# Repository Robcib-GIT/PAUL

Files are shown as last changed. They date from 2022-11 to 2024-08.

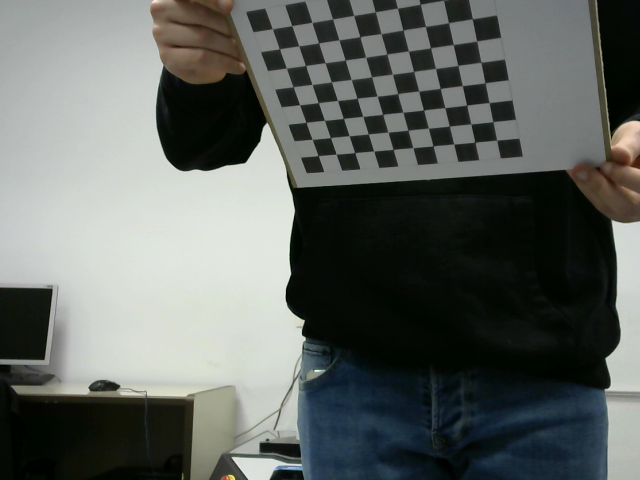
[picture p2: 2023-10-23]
Docs/Assets/Raúl/Calibracion/Fotos/Image35.png

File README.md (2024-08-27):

# Pneumatic Actuated Ultrasoft Limb (PAUL)

In this repository you will find all the code necessary for the control of the PAUL soft robot. Due to the problems that can be associated with working with it and the difficulty of building it, it is also possible to work using a built-in simulator. The programming language used is Matlab.





## Available videos ##

- [Manufacturing Process](https://www.youtube.com/watch?v=WlBE3JDpxWw)
- [General Working](https://www.youtube.com/watch?v=1XM6AjTwlqs)
- [One Module Control](https://www.youtube.com/watch?v=sqhGBfGOFts)

## Inverse Kinematics ##

We are currently working on the development of several inverse kinematics methods. We will post updates here when they reach a first functional level.

Although we are open to explore different possibilities, we consider, for the moment, to use optimisation-based algorithms (such as CCD or FABRIK), search methods (type A*), genetic algorithms and, of course, reinforcement learning.

### Genetic Algorithm

The algorithm developed here achieves errors of less than 1mm with execution times fast enough for soft robots. Contrary to what happens in many methodologies, the algorithm allows the position of the robot's intermediate modules to be chosen.

The hyperparameters have been decided starting from those established [in this work](https://www.mdpi.com/2075-1702/11/10/952) and then making small variations with the aim of finding a solution capable, at the same time, of achieving good precision in low times.

The following table shows the results of the hyperparameter optimisation. The number of individuals and elitism and mutation rates have been varied. For each hyperparameter setup, the algorithm has been runned 40 times. For all of them, median error and execution time have been compared for the genetic algorithm without shape control.

<details>
  <summary><strong>Hyperparameter optimisation table</strong></summary>
  <table>
    <thead>
    <tr>
    <th># of individuals</th>
    <th>Parents&#39; rate</th>
    <th>Mutation rate</th>
    <th>Median error (mm)</th>
    <th>Median time (s)</th>
    </tr>
    </thead>
    <tbody>
    <tr>
    <td>25</td>
    <td>0.1</td>
    <td>0.7</td>
    <td>1.30</td>
    <td>3.68</td>
    </tr>
    <tr>
    <td>25</td>
    <td>0.1</td>
    <td>0.8</td>
    <td>1.33</td>
    <td>3.91</td>
    </tr>
    <tr>
    <td>25</td>
    <td>0.2</td>
    <td>0.7</td>
    <td>1.31</td>
    <td>3.42</td>
    </tr>
    <tr>
    <td>25</td>
    <td>0.2</td>
    <td>0.8</td>
    <td>1.36</td>
    <td>3.42</td>
    </tr>
    <tr>
    <td>25</td>
    <td>0.3</td>
    <td>0.7</td>
    <td>1.07</td>
    <td>3.05</td>
    </tr>
    <tr>
    <td>25</td>
    <td>0.3</td>
    <td>0.8</td>
    <td>1.99</td>
    <td>3.14</td>
    </tr>
    <tr>
    <td>50</td>
    <td>0.1</td>
    <td>0.7</td>
    <td>0.91</td>
    <td>6.19</td>
    </tr>
    <tr>
    <td>50</td>
    <td>0.1</td>
    <td>0.8</td>
    <td>0.90</td>
    <td>4.56</td>
    </tr>
    <tr>
    <td><strong>50</strong></td>
    <td><strong>0.2</strong></td>
    <td><strong>0.7</strong></td>
    <td><strong>0.88</strong></td>
    <td><strong>4.31</strong></td>
    </tr>
    <tr>
    <td>50</td>
    <td>0.2</td>
    <td>0.8</td>
    <td>0.88</td>
    <td>4.81</td>
    </tr>
    <tr>
    <td>50</td>
    <td>0.3</td>
    <td>0.7</td>
    <td>0.99</td>
    <td>6.12</td>
    </tr>
    <tr>
    <td>50</td>
    <td>0.3</td>
    <td>0.8</td>
    <td>0.90</td>
    <td>5.03</td>
    </tr>
    <tr>
    <td>75</td>
    <td>0.1</td>
    <td>0.7</td>
    <td>0.86</td>
    <td>5.40</td>
    </tr>
    <tr>
    <td>75</td>
    <td>0.1</td>
    <td>0.8</td>
    <td>0.82</td>
    <td>5.37</td>
    </tr>
    <tr>
    <td>75</td>
    <td>0.2</td>
    <td>0.7</td>
    <td>0.84</td>
    <td>5.75</td>
    </tr>
    <tr>
    <td>75</td>
    <td>0.2</td>
    <td>0.8</td>
    <td>0.71</td>
    <td>5.95</td>
    </tr>
    <tr>
    <td>75</td>
    <td>0.3</td>
    <td>0.7</td>
    <td>0.82</td>
    <td>6.52</td>
    </tr>
    <tr>
    <td>75</td>
    <td>0.3</td>
    <td>0.8</td>
    <td>0.85</td>
    <td>6.58</td>
    </tr>
    <tr>
    <td>100</td>
    <td>0.1</td>
    <td>0.7</td>
    <td>0.79</td>
    <td>5.17</td>
    </tr>
    <tr>
    <td>100</td>
    <td>0.1</td>
    <td>0.8</td>
    <td>0.83</td>
    <td>5.14</td>
    </tr>
    <tr>
    <td>100</td>
    <td>0.2</td>
    <td>0.7</td>
    <td>0.74</td>
    <td>5.79</td>
    </tr>
    <tr>
    <td>100</td>
    <td>0.2</td>
    <td>0.8</td>
    <td>0.83</td>
    <td>7.02</td>
    </tr>
    <tr>
    <td>100</td>
    <td>0.3</td>
    <td>0.7</td>
    <td>0.81</td>
    <td>8.19</td>
    </tr>
    <tr>
    <td>100</td>
    <td>0.3</td>
    <td>0.8</td>
    <td>0.87</td>
    <td>7.55</td>
    </tr>
    </tbody>
  </table>
 
</details>

## Directory index ##

- Code_arduino: Arduino code for controlling the pneumatic actuation bench, which sends the necessary compressed air to move the robot.
- Code_matlab: Matlab code. It includes the control interface, where one can control everything related to computer vision, communications between the robot and the computer, the actuation signals, etc.
- CAD: Everything related to the CAD designs, from the molds to the joints of the robot. They were designed using Autodesk Fusion 360.
- Memoria: Everything related to the thesis documentation.

## Published works ##

García-Samartín, J.F.; Rieker, A.; Barrientos, A. Design, Manufacturing, and Open-Loop Control of a Soft Pneumatic Arm. _Actuators_ **2024**, 13, 36. https://doi.org/10.3390/act13010036

García-Samartín, J.F.; Molina-Gómez, R.; Barrientos, A. Model-Free Control of a Soft Pneumatic Segment. _Biomimetics_ **2024**, 9, 127. https://doi.org/10.3390/biomimetics9030127

García-Samartín, J.F., del Cerro, J., Barrientos, A. Inverse kinematic modelling with shape control of a soft robot using genetic algorithms. _Jornadas de Automática_ **2024**, 45. https://doi.org/10.17979/ja-cea.2024.45.10968

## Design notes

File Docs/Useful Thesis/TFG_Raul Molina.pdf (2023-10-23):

# SENSORIZACIÓN Y CONTROL DE UN ROBOT BLANDO

# MANIPULADOR

SEPTIEMBRE 2023

## Raúl Molina Gómez

DIRECTORES DEL TRABAJO FIN DE GRADO:

## Antonio Barrientos Cruz Jorge F. García-Samartín

## Raúl Molina Gómez

### TRABAJO FIN DE GRADOPARA LA OBTENCIÓN DEL TÍTULO DE GRADUADO EN INGENIERÍA EN TECNOLOGÍAS INDUSTRIALES

### Universidad Politécnica de Madrid

### Escuela Técnica Superior de Ingenieros Industriales

## Grado en Ingeniería en Tecnologías Industriales

### Trabajo Fin de Grado

## Sensorización y Control de un Robot Blando Manipulador

### Autor: Raúl Molina Gómez

### Tutor Académico: Antonio Barrientos Cruz

### Cotutor: Jorge F. García-Samartín

### septiembre, 2023

ii

# Agradecimientos

En primer lugar, quiero expresar mi agradecimiento a todas las personas cuyo apoyo ha sido muy valioso para mí tanto durante la realización de este proyecto como durante todos mis estudios universitarios.
Agradezco a mis padres por haberme brindado siempre la mejor educación posible, por haberme ayudado cuando más lo necesitaba y por los excelentes valores personales basados en el esfuerzo, el respeto y la humildad que me han inculcado.
Agradezco a mi hermana por su ayuda y apoyo durante toda la carrera universitaria. Agradezco también a todos mis amigos y compañeros de carrera, pues sin ellos no sería quien soy actualmente.

Asimismo, quiero agradecer a todas aquellas personas que me han ayudado a llevar a cabo este proyecto.
Agradezco a Antonio Barrientos, por confiar en mí y darme la oportunidad de realizar este Trabajo Fin de Grado en el laboratorio Robcib. También quiero agradecer su ayuda y la motivación que me ha dado en los momentos de mayor desesperación.
Agradezco de manera especial a Jorge García-Samartín por su paciencia, amabilidad, tiempo y guía durante este trabajo. Sin ti no habría sido posible completar este proyecto. Agradezco también a todos los que me habéis acompañado durante toda la realización del proyecto en el laboratorio Robcib. Chrystian, David e Ysmaldo, me habéis acogido como un doctorando más y me habéis ayudado a conseguir este logro creando un clima de trabajo extraordinario.

Raúl Molina Gómez

iii

# Resumen Ejecutivo

En la actualidad, el desarrollo de nuevos robots que permitan realizar y automatizar cada vez más tareas se ha convertido en una prioridad en la industria robótica. Estas investigaciones se enfocan tanto en nuevos sistemas de control como en el diseño y fabricación de robots con nuevos materiales. Es así como surge hace aproximadamente 20 años un nuevos campo de la robótica: la robótica blanda o Soft Robotics.

Este nuevo tipo de robots surge con el objetivo de crear máquinas cuyas propiedades y comportamiento se asemejen a los organismos biológicos y tejidos blandos. Este nuevo enfoque se aleja completamente del concepto de robótica que se venía empleando en las épocas pasadas, pues no se usan para su construcción materiales rígidos.

Estos factores en su diseño y estructura les otorgan una gran ventaja: son capaces de interactuar de manera segura y eficiente con entornos cambiantes y complejos. Esto permite su uso en múltiples aplicaciones hasta ahora extremadamente complejas de realizar, como el trabajo con humanos o la adaptación a terrenos de difícil acceso para un robot móvil tradicional. Un ejemplo de esto último serían los escombros de un edificio o tuberías estrechas y serpenteantes.

Son todas estas potenciales aplicaciones para la sociedad las que motivan la investigación acerca de esta nueva tecnología, como es el caso de este proyecto. Así, el objetivo que presenta este Trabajo Fin de Grado es el de realizar sobre el diseño del Robot PAUL, fruto del trabajo de Adrián Rieker [1], un sistema de control en posición en cadena cerrada para uno de los segmentos que lo componen. Para ello se precisa además modificar ciertos aspectos del robot, como su diseño o proceso de fabricación, así como seleccionar y caracterizar el método de sensorización a emplear.

Cabe señalar que el Robot PAUL se compone de varios módulos blandos en serie, cada uno de los cuales es actuado mediante 3 vejigas neumáticas que, al deformarse por efecto del aire a presión que se introduce en ellas, consiguen modificar la forma del módulo. Para lograrlo, y debido a la falta de sensores de presión, la cantidad de aire comprimido introducido en cada módulo se regula mediante el tiempo de apertura de los circuitos de

v

vi RESUMEN EJECUTIVO

admisión y escape del aire. A este tiempo de apertura se le ha denominado como tiempo de actuación.
Para completar el bucle de control en cadena cerrado se han empleado unos sensores resistivos elastómeros comerciales (figura R1), fabricados por la empresa Adafruit [2]. Estos sensores permiten medir cambios en sus resistencias producidos por variaciones en su longitud. De esta forma, se mide de manera indirecta la deformación y forma final de cada uno de los segmentos del robot a los que están fijos.

Figura R1 Sensores empleados para el sistema de control en cadena cerrada del robot. Fuente [2]

Estas medidas se realizan gracias a un hardware específico de medición y monitoreo de parámetros eléctricos denominado INA3221. Este dispositivo permite obtener medidas de tensión, corriente y/o potencia con elevada precisión gracias a un filtro paso bajo y un convertidor analógico-digital. Además, cuenta con tres canales de medida, con lo que se pueden realizar mediciones de los tres sensores que incorpora cada segmento. Así, la técnica empleada consiste en alimentar mediante una fuente de tensión un divisor de tensiones compuesto por una resistencia fija y un sensor, lo que permite medir las variaciones de tensión que sufre el sensor cuando se produce la actuación y correspondiente deformación del segmento.
Asimismo, para la caracterización de los sensores se ha diseñado y construido un banco de pruebas (figura R2) que estira de manera constante y uniforme el sensor. De esta forma se puede extraer la relación entre la tensión medida y su variación de longitud. A su vez, para su fijación e implementación en el robot, se ha usado un sellador adhesivo de silicona denominado comercialmente DOWSIL 732.

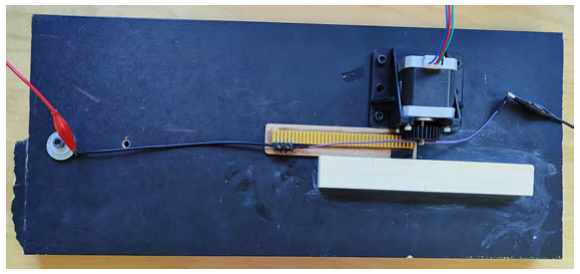
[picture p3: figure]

Figura R2 Banco de pruebas diseñado para caracterizar el comportamiento de los sensores. Fuente: elaboración propia

SENSORIZACIÓN Y CONTROL DE UN ROBOT BLANDO MANIPULADOR RAÚL MOLINA GÓMEZ

RESUMEN EJECUTIVO vii

Por su parte, el sistema de control emplea el diagrama de bloques de la figura R3 para que, mediante la introducción de un punto objetivo contenido en el espacio de trabajo del robot, se consiga mover dicho robot al punto deseado obteniendo un error mínimo. Este sistema surge como resultado de numerosas pruebas e iteraciones de búsqueda y perfeccionamiento del método de control adecuado. La justificación a este largo proceso es la complejidad presente en el modelado de los Soft Robots, pues su estructura continua y maleable les otorga una característica nunca vista en la robótica tradicional que es la inexistencia de cadena cinemática, o lo que es lo mismo, se podría considerar que estos robots presentan infinitos grados de libertad.

Figura R3 Diagrama de bloques empleado para el control del segmento. Fuente: elaboración propia

La resolución a este problema finalmente pasa por el entrenamiento de dos redes neuronales prealimentadas o feedfoward. En el caso de la primera de ellas (la denominada como NN1), transforma los valores de posición introducidos en tiempos de actuación objetivo, mientras que la segunda (NN2) convierte las mediciones de tensión en tiempos de actuación del robot. Así, se suprime la necesidad de un regulador multivariable. Para su obtención, es necesario realizar el entrenamiento de las redes usando múltiples datos contenidos en datasets del comportamiento del robot. Así, se ha diseñado además un método de obtención de estos datos (tensiones, posiciones y tiempos) de forma automática, basado en el método de captura de posiciones por visión con computador ideado por Adrián Rieker [1]. Uno de los resultados de esta captura de datos se ve en la figura R4, que muestra el espacio de trabajo del robot.

Figura R4 Espacio de trabajo del robot desarrollado. Fuente: elaboración propia

UNIVERSIDAD POLITÉCNICA DE MADRID ESCUELA TÉCNICA SUPERIOR DE INGENIEROS INDUSTRIALES

viii RESUMEN EJECUTIVO

Durante esta fase del proyecto, se observaron además múltiples problemas relacionados con el diseño y la fabricación del robot, como las numerosas fugas de aire que se producían. Es por ello que se acometieron como un objetivo adicional del trabajo modificaciones en el diseño, la programación y el proceso de fabricación del robot.
Finalmente, y tras las numerosas iteraciones de obtención de datos y diseño y entrenamiento de las redes, se procedió a realizar varias pruebas y experimentos para verificar el cumplimiento de los objetivos. Los resultados obtenidos fueron muy satisfactorios, logrando errores de en torno a los 5mm, obteniendo así un robot que incluso supera en precisión a otros robots similares desarrollados en la literatura.
Con todo ello, el trabajo final realizado se puede ver en la figura R5.

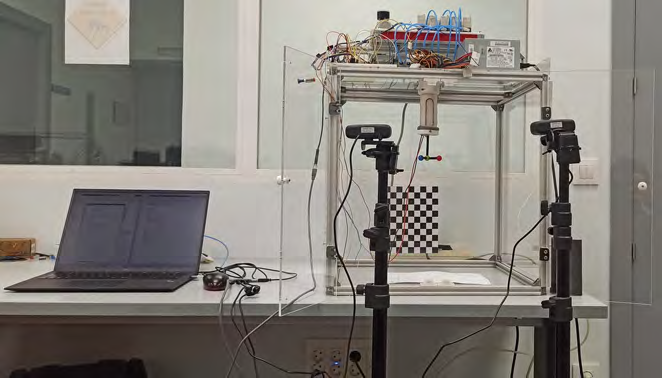
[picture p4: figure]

Figura R5 Imagen del entorno del robot durante su desarrollo. Fuente: elaboración propia

Códigos UNESCO

1203 Ciencia de los ordenadores 1203.04 Inteligencia Artificial 1203.25 Diseño de sistemas sensores 3304 Tecnología de los ordenadores 3304.12 Dispositivos de control
3304.19 Robótica
3311 Tecnología de la Instrumentación 3311.01 Tecnología de la automatización 3311.02 Ingeniería de control
3311.07 Instrumentos electrónicos

Palabras clave

Robótica blanda, Soft Robot, manipulador, sensor resistivo elastómero, red neuronal, feedforward neuronal network, control en posición, MATLAB, Arduino, silicona.

SENSORIZACIÓN Y CONTROL DE UN ROBOT BLANDO MANIPULADOR RAÚL MOLINA GÓMEZ

# Índice

Índice de Figuras | xvi
Índice de Tablas | xvii
1. Introducción | 1
2. Estado del arte | 7
2.2.3. Métodos experimentales. Métodos basados en el entrenamiento de
3. Estudio y caracterización de los sensores | 29

ix

x RESUMEN EJECUTIVO

3.3. Caracterización del comportamiento de los sensores | 36
3.3.1. Cambio de comportamiento de los sensores | 36
3.3.2. Diseño y construcción del banco de pruebas | 39
3.3.3. Conclusiones extraídas del comportamiento de los sensores | 43
3.4. Instrumentación final e implementación de los sensores en el robot | 45
3.4.1. Justificación de la elección del método de fijación de los sensores . . 45
3.4.2. Instrumentación y montaje final | 48
4. Herramientas utilizadas | 51
4.1. Deep Learning Toolbox de MATLAB | 51
4.2. Redes Neuronales Prealimentadas (Feedforward Neural Network) | 53
4.2.1. Funcionamiento de una red neuronal prealimentada | 53
4.2.2. Redes Neuronales Feedforward en MATLAB | 57
4.3. Redes Neuronales de tipo LTSM | 59
4.3.1. Arquitectura Básica de una Celda LSTM | 60
4.3.2. Implementación Práctica en MATLAB | 61
5. Modificaciones del diseño, fabricación y control de los segmentos | 63
5.1. Cambios en el proceso de fabricación | 63
5.1.1. Cambio de posición de las vejigas | 64
5.1.2. Método de sellado de fugas | 65
5.1.3. Eliminación del espacio interno del segmento | 66
5.1.4. Cambio de forma de los machos de cera | 67
5.2. Cambios en el diseño | 68
5.2.1. Nuevas piezas | 69
5.3. Cambios en la forma de control del robot | 72
6. Diseño y desarrollo del sistema de control para un segmento | 75
6.1. Introducción | 75
6.2. La clase Robot | 75
6.2.1. Código Arduino | 80
6.3. Planteamiento inicial del problema - Control analítico | 82
6.4. Segundo intento de resolución del problema - Control experimental . . . . 85
6.4.1. Obtención de la red neuronal a emplear | 86
6.4.2. Diseño del regulador PID | 93
6.4.3. Conclusiones | 94
6.5. Resolución y planteamiento final del problema | 95
6.5.1. Esquema de control final | 95
6.5.2. Obtención de la red neuronal a emplear | 96
6.5.3. Conclusiones y resultados | 98

SENSORIZACIÓN Y CONTROL DE UN ROBOT BLANDO MANIPULADOR RAÚL MOLINA GÓMEZ

ÍNDICE xi

6.5.4. Descarte del uso de redes LSTM | 99
6.6. Control del robot | 100
6.6.1. Métodos para el movimiento del segmento | 100
6.6.2. Procedimiento de uso | 102
7. Pruebas y Resultados | 103
7.1. Experimentos de posicionamiento | 104
7.1.1. Primer experimento | 104
7.1.2. Segundo experimento | 105
7.1.3. Tercer experimento | 107
7.2. Experimentos de estudio de la modularidad | 109
8. Conclusiones y líneas futuras | 113
8.1. Conclusiones | 113
8.2. Líneas futuras | 115
Bibliografía | 117
A. Estudio de impacto ambiental, social, ético y legal | 123
A.1. Impacto ambiental | 123
A.1.1. Impacto social | 125
A.1.2. Impacto ético | 125
A.1.3. Impacto legal | 126
A.1.4. Conclusión: ODS | 126
B. Planificación temporal y presupuesto | 127
B.1. Estructura de Descomposición del Proyecto | 127
B.2. Planificación | 128
B.3. Presupuesto | 129
B.3.1. Coste material | 129
B.3.2. Coste de amortización | 129
B.3.3. Coste de personal | 130
B.3.4. Presupuesto final | 130
C. Código de interés | 131

UNIVERSIDAD POLITÉCNICA DE MADRID ESCUELA TÉCNICA SUPERIOR DE INGENIEROS INDUSTRIALES

# Índice de Figuras

R1. Sensores empleados para el sistema de control en cadena cerrada del robot.
Fuente [2] | vi

R2. Banco de pruebas diseñado para caracterizar el comportamiento de los
sensores. Fuente: elaboración propia | vi
R3. Diagrama de bloques empleado para el control del segmento. Fuente: ela-
boración propia | vii
R4. Espacio de trabajo del robot desarrollado. Fuente: elaboración propia . . . vii R5. Imagen del entorno del robot durante su desarrollo. Fuente: elaboración
propia | viii
1.1. Aumento de las búsquedas de carácter académico relacionadas con la ro-
bótica blanda. Fuente: Scopus | | 2
1.2. Robot final desarrollado en el trabajo previo de Adrián Rieker. Fuente [1] . | 4
2.1. Clasificación de los sensores con base de hidrogel según su aplicación y
composición. Fuente [5] | 9
2.2. Comportamiento y características de un sensor fabricado con un hidrogel
orgánico. Fuente [6] | 10
2.3. Comportamiento ante el movimiento humano de un sensor hidrogelado.
Fuente [7] | 11
2.4. Propiedades de un sensor con base de hidrogel e iones de hierro. Fuente [8] 11
2.5. Estudio del comportamiento y uso de un sensor elastómero fabricado con
impresión 3D. Fuente [9] | 12
2.6. Estructura esquemática de los MXene, incluyendo los dopados con elementos de transición M y los dopados con elementos ligadores X, y los MAX
de los que provienen. Fuente [12] | 13
2.7. Resultados de un sensor capacitivo realizado con un MXene y una matriz
elastomérica. Fuente [13] | 14

xii

ÍNDICE GENERAL xiii

2.8. Resultados de un sensor flexible piezorresistivo realizado con un MXene.
Fuente [14] | 15
2.9. Ejemplo de funcionamiento de un sensor óptico empleado en robótica blan-
da. Fuente [16] | 16
2.10. Ejemplo de funcionamiento de un sensor magnético empleado en robótica
blanda. Fuente [17] | 17
2.11. Ejemplo de uso y caracterización de un sensor inductivo aplicado a la ro-
bótica blanda. Fuente [18] | 18
2.12. Creación, uso y validación de un sensor basado en corrientes de Foucault.
Fuente [19] | 19
2.13. Los dos pasos necesarios para el modelado de robots blandos: modelado específico (entre el espacio de los actuadores y el de las configuraciones)
y modelado independiente (entre el espacio de configuraciones y el de la
tarea). Fuente [20] | 19
2.14. Principales métodos para el modelado de Soft Robots. Fuente [21] | 21
2.15. Principales métodos para el control de Soft Robots. Fuente [21] | 21
2.16. Modelado y control mediante elementos finitos. Fuente [22] | 22
2.17. Modelado basado en curvatura constante. Fuente [23] | 23
2.18. Control de un Soft Robot actuado con tendones mediante el uso de la teoría
de vigas de Cosserat. Fuente [24] | 24
2.19. Resultados de una simulación realizada para un robot blando manipulador utilizando un modelo basado en la curvatura polinómica de 4º grado. Fuente
[25] | 25
2.20. Resultados del empleo de una red neuronal para conocer la posición de
un robot blando a partir de las medidas de sus sensores de deformación.
Fuente [27] | 26
2.21. Robot blando y su setup para el control con el uso de PCC y aprendizaje
por refuerzo. Fuente [28] | 27
3.1. Sensor resistivo elastómero empleado en el control en cadena cerrada de
PAUL. Fuente [2] | 30
3.2. Microcontrolador Arduino Due empleado. Fuente: elaboración propia . . . 32
3.3. Ruido de la señal medida y su solución por filtrado. Fuente: elaboración
propia | 33
3.4. Selección del hardware de medición. Fuente [29], [30] y [31] | 35
3.5. Comportamiento de un sensor similar al empleado en este proyecto. Fuente
[32] | 38
3.6. Comparación del comportamiento de los sensores comercial y modificado.
Fuente: elaboración propia | 38

UNIVERSIDAD POLITÉCNICA DE MADRID ESCUELA TÉCNICA SUPERIOR DE INGENIEROS INDUSTRIALES

xiv ÍNDICE GENERAL

3.7. Par piñón-cremallera empleado en el banco de pruebas para caracterizar el
3.8. Base de apoyo para anclar y fijar el motor paso a paso en el banco de
3.9. Sistema de anclaje del extremo fijo del sensor a probar. Fuente: elaboración
3.10. Detalles de las conexiones de ambos extremos del sensor a caracterizar.
3.11. Guía para evitar el movimiento lateral de la cremallera. Fuente: elaboración
3.12. Banco de pruebas para la caracterización de los sensores. Fuente: elabora-
3.13. Comportamiento ante la elongación de dos sensores modificados distintos.
3.14. Comportamiento de uno de los sensores modificados ante las distintas tem-
3.15. Sellador de silicona empleado en la fijación de los sensores al robot. Fuente
3.16. Molde y pieza para la prueba de la fijación del sensor a la silicona con el
3.17. Detalle de la fijación de los sensores con el sellador Dowsil 732. Fuente:
3.18. Posición de todos los elementos electrónicos para el posterior control del
3.19. Detalle de las conexiones entre dispositivo de medida y sensor. Fuente:
3.20. Esquema de la conexión entre los dispositivos. Fuente: elaboración propia
4.1. Modelo computacional de red neuronal prealimentada de una sola capa
4.5. Ejemplo de función de costo respecto a los pesos y sesgos de las neuronas.

SENSORIZACIÓN Y CONTROL DE UN ROBOT BLANDO MANIPULADOR RAÚL MOLINA GÓMEZ

ÍNDICE GENERAL xv

4.6. Estructura de una celda de una red neuronal recurrente LSTM, donde los valores de c son los correspondientes a la memoria, h representa las salidas y x las entradas. Las celdas en amarillo son redes neuronales simples con sus funciones de activación y los puntos rosa son operaciones específicas para descartar, actualizar y calcular el nuevo estado oculto de la memoria.
5.1. Comparación de la posición de las cámaras internas de PAUL antes y después de su cambio. Su ubicación se puede deducir a partir de los salientes superiores para introducir los tubos neumáticos que conducen el aire a su
5.2. Detalle de la parte inferior de un segmento. Fuente: elaboración propia . . 65
5.3. Detalle de la fijación de los tubos neumáticos a un segmento del robot.
5.4. Detalle del moldeo de un segmento sin cavidad interna. Fuente: elaboración
5.5. Comparación entre la geometría nueva y antigua de los machos de cera que
5.6. Comparación entre los diseños antiguo y nuevo de la pieza de conexión con
5.8. Comparación entre los diseños antiguo y nuevo de la pieza de conexión
5.9. Comparación entre los diseños antiguo y nuevo de la baliza de captura de
6.3. Esquema de control empleando tabla dinámica y MCI. Fuente: elaboración
6.4. Esquema de control empleando una red neuronal y un regulador PID. Fuen-
6.5. Diagrama del proceso de obtención de datos. Fuente: elaboración propia . . 90
6.6. Diagrama de bloques empleado para el control del segmento. Fuente: ela-
6.7. Diagrama final del proceso de obtención de datos. Fuente: elaboración propia 97
6.8. Resultados del entrenamiento de dos redes LSTM. Fuente: elaboración propia 99

UNIVERSIDAD POLITÉCNICA DE MADRID ESCUELA TÉCNICA SUPERIOR DE INGENIEROS INDUSTRIALES

xvi ÍNDICE DE FIGURAS

7.2. Robot PAUL durante el primer experimento de verificación de su capacidad
7.4. Espacio de trabajo de un segmento del robot PAUL. Fuente: elaboración
7.5. Movimientos realizados por el robot durante el tercer experimento. Fuente:
7.6. Robot PAUL durante el primer experimento del estudio de modularidad.
7.7. Robot PAUL durante el segundo experimento del estudio de modularidad.
7.8. Piezas necesarias para la fabricación de la nueva baliza. Fuente: elaboración

A.1. ODS a los que contribuye este proyecto. Fuente: elaboración propia . . . . 126

B.1. Estructura de Descomposición del Proyecto. Fuente: elaboración propia . . 127

SENSORIZACIÓN Y CONTROL DE UN ROBOT BLANDO MANIPULADOR RAÚL MOLINA GÓMEZ

# Índice de Tablas

3.1. Tabla comparativa de las distintas características del INA219, el INA226 y
el INA3221. Fuente: Elaboración propia | 34
3.2. Principales propiedades del sellador DOWSIL 732 Multi-Purpose Sealant.
Fuente: Adaptación de [34] | 46
7.1. Resultados del primer experimento. Fuente: elaboración propia | 105
7.2. Resultados del segundo experimento. Fuente: elaboración propia | 105
7.3. Resultados de la prueba de realización de figuras. Fuente: elaboración propia 109
7.4. Resultados del experimento con un segmento adicional. Fuente: elaboración
propia | 111
7.5. Resultados del experimento con dos segmentos adicionales. Fuente: elabo-
ración propia | 111
B.1. Coste de material | 129
B.2. Coste de amortización del proyecto | 130
B.3. Coste de personal colaborador del proyecto | 130
B.4. Presupuesto total del proyecto | 130

xvii

Capítulo1

# Introducción

Desde la aparición de los primeros homínidos, el ser humano siempre ha mostrado un gran interés por idear métodos que permitieran realizar las tareas más complejas de una forma sencilla. Es gracias a esta necesidad de avance lo que permitió la invención de la rueda, la fabricación de las primeras herramientas de trabajo o la construcción de las primeras edificaciones modernas.

No será sin embargo hasta la Revolución Industrial cuando el ser humano verá en la automatización de los procesos una necesidad para lograr mayores avances en la sociedad. Es así como surgen los primeros robots, en forma de computadoras analíticas, que permitían la realización de cálculos matemáticos a una velocidad muy superior a la del ser humano. Fue gracias al desarrollo de las computadoras durante el siglo XX lo que permitió finalmente el desarrollo de los primeros robots industriales, dotados de mecanismos que permitían la realización de las tareas manuales de un humano a una velocidad asombrosa.

Desde entonces, los robots están presenten en todas las facetas de la vida, desde la fabricación de un automóvil o el transporte de las personas hasta la limpieza del hogar o, incluso, el cocinado de alimentos. Es precisamente esta capacidad de adaptación a las distintas tareas las que han motivado desde su aparición el desarrollo de nuevos robots.

Es gracias a la investigación de nuevos tipos de robots lo que permitirá en el año 2000 la aparición de los primeros robots blandos (Soft Robots) en el mundo. Desde entonces, la robótica blanda se ha convertido en una de las tendencias que más interés genera entre la comunidad científica, como muestra la figura 1.1.

1

TRABAJO FIN DE GRADO
SENSORIZACIÓN Y CONTROL DE UN ROBOT BLANDO MANIPULADOR - RAÚL MOLINA GÓMEZ

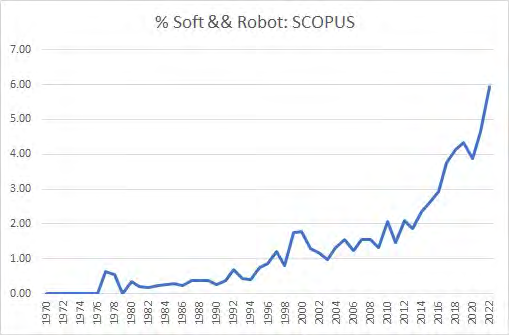
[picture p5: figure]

Figura 1.1 Aumento de las búsquedas de carácter académico relacionadas con la robótica blanda. Fuente: Scopus

Este nuevo campo de la robótica busca crear robots y dispositivos con propiedades y características similares a las de los organismos biológicos y tejidos blandos. Esto se aleja completamente del concepto de robótica que se venía empleando en las épocas pasadas, pues no se emplean para su construcción materiales rígidos.
Esta estructura flexible otorgan a estos robots unas cualidades excepcionales que justifican su construcción y desarrollo. Una de ellas es su estructura blanda, pues a diferencia de los robots rígidos convencionales, los robots blandos están diseñados para ser flexibles, por lo que son capaces de interactuar de manera segura y eficiente con entornos cambiantes y complejos. Esto les permite trabajar en conjunción con humanos reduciendo al mínimo los accidentes laborales. Además, su estructura maleable les permite introducirse en huecos y adaptarse a terrenos en los que un robot móvil tendría dificultades en la accesibilidad, como en los escombros tras el derrumbamiento de un edificio o en la exploración de tuberías.
Son todos estos aspectos los que motivan su desarrollo y justifican su creciente investigación tanto en universidades como en empresas del sector de la robótica.

## 1.1. Motivación

La robótica blanda (Soft Robotics), es un área reciente de la robótica que ha cobrado gran interés por sus ventajas en determinadas aplicaciones, como en aquellas donde hay un contacto directo con seres vivos. Su desarrollo presenta retos complejos, tanto en lo relativo a su fabricación (materiales, modos constructivos,...), como a su actuación (actuadores blandos) y control, pues su falta de rigidez origina que el movimiento del actuador y el robot estén en cierta medida desacoplados.
En el Centro de Automática y Robótica (CAR) se ha abordado el desarrollo y control de diferentes tipologías de robots blandos. Una de ellas es la de robots manipuladores con accionamiento neumático. Como resultado de ello se cuenta con algún prototipo funcional

2 INTRODUCCIÓN

UNIVERSIDAD POLITÉCNICA DE MADRID ESCUELA TÉCNICA SUPERIOR DE INGENIEROS INDUSTRIALES

de robot y de sus sistema de accionamiento. Su control, sin embargo, es aún incipiente, realizándoselo en cadena abierta en base a un modelo no explicito, obtenido experimentalmente y formulado mediante una red neuronal. Para avanzar en la investigación en robótica blanda en general y en particular en el control del robot manipulador, es preciso avanzar en su control, utilizando la realimentación de su localización y evaluando diferentes opciones de técnicas de control en cadena cerrada.
Son estos retos los que motivan el desarrollo de este proyecto, pues sus aplicaciones futuras pueden ser ampliamente variadas. Además, el trabajo aquí realizado puede ayudar al desarrollo de la industria de la robótica blanda y de la sociedad en un futuro.

## 1.2. Objetivos

Este trabajo tiene como finalidad el diseño, desarrollo y verificación de un sistema de control para el robot neumático desarrollado por Adrián Siegbert Rieker [1]. Este sistema debe ser capaz de posicionar el extremo del robot con la mayor precisión posible.
Para lograrlo, es necesario además realizar la caracterización y selección de los sensores que permitan cerrar el bucle de control en cadena cerrada y su implementación en el robot. Para ello, se espera realizar cambios en su diseño y técnica de fabricación. Adicionalmente, se desea estudiar su aplicabilidad a futuros proyectos de desarrollo del control del robot de forma modular o segmentada.
De esta forma, los objetivos del Trabajo Fin de Grado se pueden resumir en los siguiente puntos:

Diseño y desarrollo de un sistema de control en posición en cadena cerrada.

Verificación del funcionamiento de dicho sistema de control.

Selección y caracterización de los sensores que permiten el bucle de control.

Implementación de los sensores en el robot.

Rediseño del método de fabricación de los segmentos para solventar problemas surgidos y adaptarlos a las necesidades actuales.

Estudio de la aplicabilidad a futuros proyectos de desarrollo del control del robot de forma modular o segmentada.

## 1.3. Proyectos relacionados - El robot PAUL

Para la realización de este proyecto se ha empleado el robot llamado PAUL diseñado por Adrián Rieker durante su Trabajo Fin de Grado [1]. Es por ello que en muchas

OBJETIVOS 3

TRABAJO FIN DE GRADO
SENSORIZACIÓN Y CONTROL DE UN ROBOT BLANDO MANIPULADOR - RAÚL MOLINA GÓMEZ

ocasiones durante el trascurso de esta memoria se darán por supuestas determinadas características o factores del robot.
Entre los avances ya realizados para este robot se encuentran:

El diseño y método de fabricación de los segmentos uq ecomponen el robot.

Los diseños de las piezas que se emplean como moldes en la fabricación del robot.

Los diseños de las piezas que unen los distintos segmentos del robot, así como las piezas que permiten sujetar el robot al utillaje externo.

El utillaje que actúa como soporte del robot. Este se componía inicialmente de una estructura formada por perfiles de aluminio. Posteriormente, Antonio Barrientos junto a los doctorandos Jorge García-Samartín e Ysmaldo Landáez diseñaron y montaron sobre dicho utillaje unas placas de metacrilato que actuaban como cerramiento y protección del robot.

El banco de actuación, conformado por electroválvulas que permiten el hinchado o deshinchado de los segmentos del robot, mosfets que se encargan de mandar las señales de apertura y cierre de las electroválvulas y un circuito neumático, incluyendo compresor y tubos neumáticos, que permiten el llenado de las cavidades del robot.

Todo el software y hardware relacionado con la visión por computador posteriormente empleada para la captura de las posiciones del extremo del robot.

El software de actuación del robot, incluyendo una interfaz de control manual y mediante tabla.

El robot final desarrollado por Adrián Rieker previo a este proyecto se puede ver en la figura 1.2.

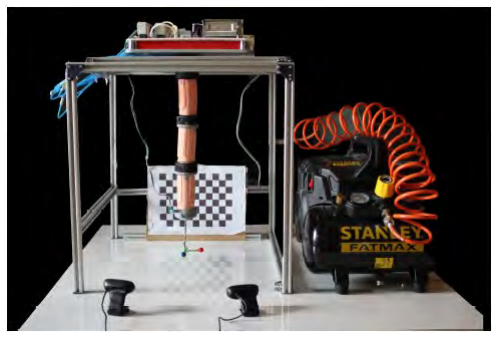
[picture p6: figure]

Figura 1.2 Robot final desarrollado en el trabajo previo de Adrián Rieker. Fuente [1]

Sobre estos avances se realizará la sensorización y el desarrollo de un sistema de control automatizado para el robot PAUL.

4 INTRODUCCIÓN

UNIVERSIDAD POLITÉCNICA DE MADRID ESCUELA TÉCNICA SUPERIOR DE INGENIEROS INDUSTRIALES

## 1.4. Estructura del trabajo

La memoria aquí expuesta engloba todos los pasos en el desarrollo de este proyecto. Esta comienza con el capítulo 2. Estado del Arte. En él, se contextualizará el trabajo realizado en este proyecto y se comentarán todos los avances y actuales tecnologías que presenta la robótica blanda (Soft Robotics) en materia de sensorización, modelado y control.
Después, con el capítulo 3: Estudio y caracterización de los sensores, se explicarán todos los requerimientos en materia de sensorización del robot, la elección de los sensores, materiales y hardware de medida necesarios y, finalmente, se expondrán los resultados obtenidos del comportamiento ante distintos estímulos.
Tras ello, se introducirá el capítulo 4: Herramientas utilizadas. En él, se explicarán con mayor detalle las herramientas de Machine Learning empleadas durante el proyecto, así como sus fundamentos teóricos.
Seguidamente, el capítulo 5: Modificaciones del diseño, fabricación y control de los segmentos, se expondrán los cambios de fabricación y diseño sobre el robot ya existente con el objetivo de solventar múltiples problemas acontecidos durante el desarrollo del trabajo.
Finalmente, en el capítulo 6: Diseño y desarrollo del sistema de control para un segmento se expondrá el desarrollo del sistema de control y su funcionamiento, comprobando su efectividad y precisión en el posicionamiento en el capítulo 7: Pruebas y resultados.
Asimismo, también se han incluido el capítulo 8: Conclusiones y líneas futuras, así como los apéndices A: Estudio del impacto ambiental y social y B: Planificación temporal y presupuesto.
Por último, se incluye en el apéndice C: Código de interés algunas de las implementaciones más relevantes en materia software del poryecto.

ESTRUCTURA DEL TRABAJO 5

Capítulo2

# Estado del arte

En este capítulo se presentarán algunos de los avances más representativos acerca de sensorización y control en el campo de la robótica blanda. También se evaluarán las aportaciones a esta industria de cada una de las técnicas empleadas en los distintos proyectos aquí expuestos.

## 2.1. Sensorización en robótica blanda

La sensorización en la robótica blanda dista mucho de la empleada en la robótica tradicional. La principal causa de este motivo es su estructura maleable y flexible, que le impide hacer uso de los sensores más comunes como, por ejemplo, encoders, acelerómetros, galgas extensiométricas o unidades de medición inercial (IMU). Es por ello que, en los últimos años y siguiendo el acelerado crecimiento de los Soft Robots en la industria robótica, se han desarrollado nuevos métodos de sensorización, utilizando muy diversos tipos de materiales.
Debido a esto, se han definido una serie de requisitos que deben cumplir los sensores utilizados en robótica blanda [3]. Estos requisitos son:
1. Permitir el movimiento del Soft Robot, sin interferir en su comportamiento normal ante los estímulos de actuación.
2. Ser lo suficientemente resilientes y flexibles para evitar roturas por fallo tras un elevado número de ciclos de movimient
3. Carecer de características que actúen como concentradores de tensiones o que puedan causar daños en la estructura del robot o en el espacio de trabajo.

Además, los valores en sus mediciones deben ser fácilmente computables y suficientemente precisos para la correcta realización de la tarea a completar por el robot.

7

TRABAJO FIN DE GRADO
SENSORIZACIÓN Y CONTROL DE UN ROBOT BLANDO MANIPULADOR - RAÚL MOLINA GÓMEZ

En este sentido, sensores con un bajo módulo elástico que permitan seguir y detectar los movimientos de flexión de los Soft Robots suelen ser la elección principal. A este grupo también pertenecen aquellos sensores que emplean materiales en fase líquida, pues poseen un alto grado de maleabilidad.
Sin embargo, han surgido otras técnicas de fabricación de sensores que emplean algunos de los materiales más avanzados y vanguardistas con el objetivo de optimizar y ampliar el abanico de posibilidades en este ámbito. Estos nuevos métodos de sensorización se pueden clasificar atendiendo al método de detección de estímulos en 6 principales grupos [4]:
1. Sensores resistivos
2. Sensores capacitivos
3. Sensores ópticos
4. Sensores magnéticos
5. Sensores inductivos
6. Sensores basados en corrientes de Foucault

### 2.1.1. Sensores resistivos

Los sensores pertenecientes a este grupo son habitualmente la primera elección cuando se trata de conocer el comportamiento y la posición de un Soft Robot.
Estos sensores poseen unas características físicas que les permiten modificar su resistividad en función de los estímulos recibidos del exterior, como cambios en la presión ejercida sobre ellos, cambios en su elongación o incluso cambios de temperatura. De esta forma, mediante la correcta intrepretación y medición de estas variaciones en la resistencia del material se puede conocer la posición e, incluso, la forma que presenta el Soft Robot. En este grupo destacan sobre el resto dos tipos de sensores, atendiendo a los materiales empleados en su fabricación: los que usan como base un hidrogel y los que utilizan materiales elastómeros como matriz.

Sensores con base hidrogelada

En la actualidad, este tipo de sensores son los más destacados. Los hidrogeles son materiales obtenidos por la combinación de un polímero y agua con estructuras tridimensionales similares a las esponjas, cuya característica principal es la posibilidad de absorber y retener grandes cantidades de agua.
Los sensores de este grupo se componen de un hidrogel, que se emplea como matriz, al que se le añaden otros materiales, principalmente micropartículas de carburos o algún otro conductor que permita su incorporación como pequeñas partículas. Existen diversos tipos que se encuentran en desarrollo a día de hoy, como se aprecia en la figura 2.1. De todos ellos, se abordarán los polímeros rellenos de partículas conductoras en esta sección y los basados en MXene en la sección 2.1.2.

8 ESTADO DEL ARTE

UNIVERSIDAD POLITÉCNICA DE MADRID ESCUELA TÉCNICA SUPERIOR DE INGENIEROS INDUSTRIALES

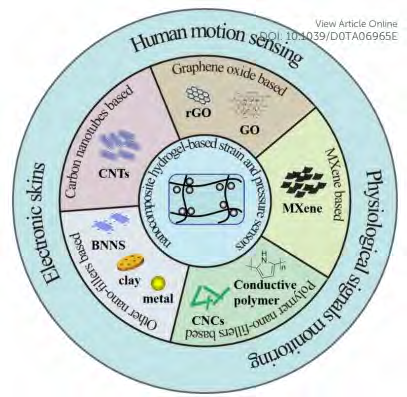
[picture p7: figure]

Figura 2.1 Clasificación de los sensores con base de hidrogel según su aplicación y composición. Fuente [5]

Los hidrogeles fabricados como polímeros conductores presentan normalmente muy buena sensibilidad, relativa buena adherencia e incluso propiedades anticongelantes o autoreparables debido a la combinación de materiales presentes en su creación. Algunos ejemplos son los trabajos realizados por [6], [7] o [8].
En el primero, se fabrica un hidrogel orgánico con una combinación de polivinilpirrolidona (PVP), ácido acrílico (AA) y acrilamida (AAm) en una disolución de agua y dimetilsulfóxido (H2O/DMSO) como solventes. Gracias a los enlaces de hidrógeno entre las cadenas de polimerización tras el curado del gel se logran muy buenas propiedades mecánicas, con una deformación de hasta un 1554 % respecto al reposo antes de la rotura, además de propiedades anticongelantes (aguantando temperaturas de hasta -40ºC) y de auto-reparabilidad. Con todo ello se logran altos grados de sensibilidad hasta un 500 % de deformación con una muy buena estabilidad térmica. Algunas de estas propiedades se pueden ver en la figura 2.2.

SENSORIZACIÓN EN ROBÓTICA BLANDA 9

TRABAJO FIN DE GRADO
SENSORIZACIÓN Y CONTROL DE UN ROBOT BLANDO MANIPULADOR - RAÚL MOLINA GÓMEZ

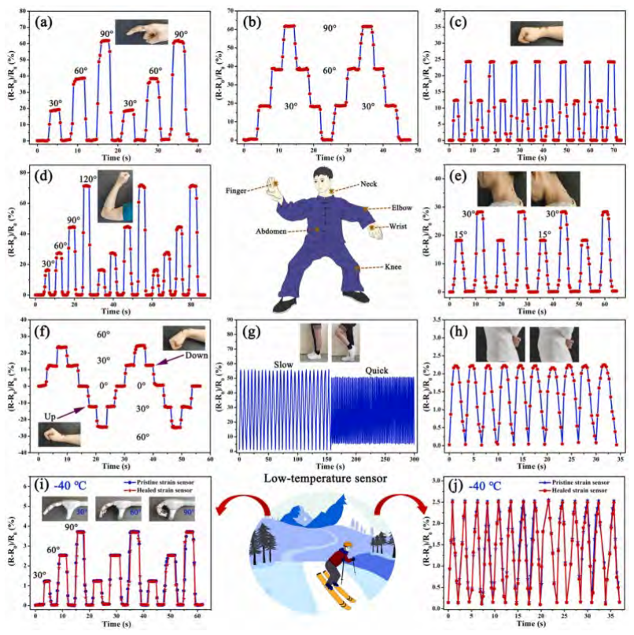
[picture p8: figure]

Figura 2.2 Comportamiento y características de un sensor fabricado con un hidrogel orgánico. Fuente [6]

En el segundo se emplea un copolímero adhesivo, conocido principalmente por su nombre abreviado P(THAM/AM), como base al que se entrecruza con nanofribras de celulosa obteniendo una matriz de gran adherencia y durabilidad. Posteriormente, se introducen iones de hierro F e³⁺, aportando al material una buena conductividad, produciendo así un sensor para medir deformacones con elevada sensibilidad y reducido tiempo de respuesta. En este proyecto además se comprobó su eficacia para detectar movimientos humanos, incluyendo algunos más amplios y otros más discretos, como se puede observar en la figura 2.3.

10 ESTADO DEL ARTE

UNIVERSIDAD POLITÉCNICA DE MADRID ESCUELA TÉCNICA SUPERIOR DE INGENIEROS INDUSTRIALES

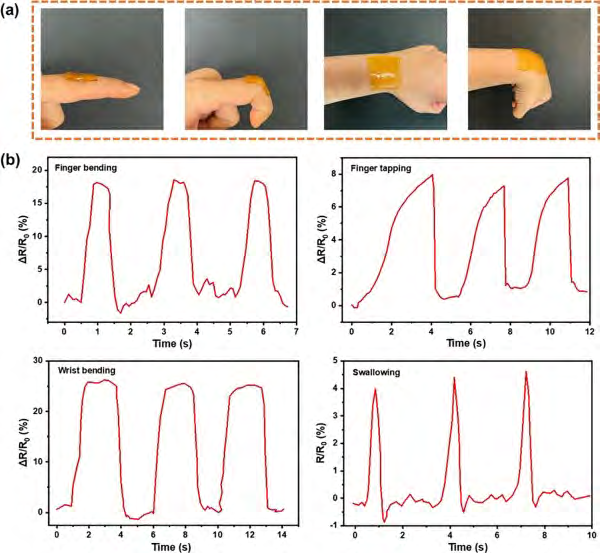
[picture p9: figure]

Figura 2.3 Comportamiento ante el movimiento humano de un sensor hidrogelado. Fuente [7]

Por último, en el tercero (figura 2.4) se crea un sensor capaz de medir tanto la temperatura como la deformación a la que está sometido. Mediante el empleo de un hidrogel con iones contenidos en su interior se consigue un sensor capaz de detectar deformaciones en un rango de hasta un 1973 % de la deformación relativa del material, además de permitir mediciones de la temperatura ambiental con resoluciones de hasta 0.2°C entre los 36.5°C y los 40°C.

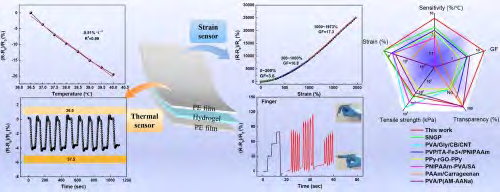
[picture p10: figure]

Figura 2.4 Propiedades de un sensor con base de hidrogel e iones de hierro. Fuente [8]

Como se ha visto, los sensores fabricados con este tipo de materiales son especialmente empleados en el modelado del movimiento humano, lo que permite extrapolar con facilidad sus aplicaciones a la robótica blanda, pues ambos tipos de comportamientos son muy similares en el método de sensorización.

SENSORIZACIÓN EN ROBÓTICA BLANDA 11

TRABAJO FIN DE GRADO
SENSORIZACIÓN Y CONTROL DE UN ROBOT BLANDO MANIPULADOR - RAÚL MOLINA GÓMEZ

Sensores con base elastomérica

Además de los sensores ya mencionados anteriormente, existen otro tipo de sensores que se vienen usando en los últimos años. Este es el caso de sensores fabricados con materiales elastómeros. En estos casos, la principal técnica de fabricación es la impresión 3D, dada la versatilidad de materias primas y formas que permite.
EL principio de funcionamiento de este tipo de sensores elásticos es muy similar a los anteriores, pues basan sus medidas en el cambio de resistividad del material al aplicar una deformación en él. Un ejemplo del empleo de estos sensores es el trabajo de [9]. En él, los investigadores Qinglei Ji et al. de la Universidad de KTH consiguen con éxito la impresión de unos sensores elásticos con los que controlarán posteriormente una garra blanda de forma precisa (figura 2.5a) gracias a las variaciones de resistencia que presenta el sensor fabricado cuando se le aplica una deformación. También se procede a un estudio de la forma óptima del sensor dependiendo del rango de detección que se desee, como se puede apreciar en la figura 2.5b.
(a) Control de una garra neumática mediante

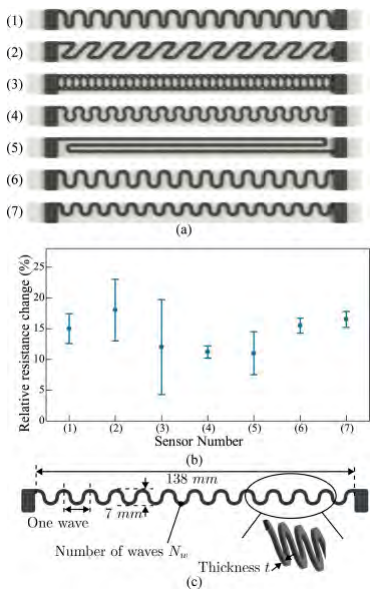
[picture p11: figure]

el uso de sensores elastómeros (en negro) | (b) Rangos de medida según la forma del sensor

Figura 2.5 Estudio del comportamiento y uso de un sensor elastómero fabricado con impresión 3D. Fuente [9]

A pesar de su mayor facilidad de fabricación y sus buenas propiedades tanto mecánicas como de sensorización, los sensores basados en elastómeros están comenzando a ser desplazados en aplicaciones relacionadas con la bioelectrónica, pues los hidrogeles, como ya se ha visto, presentan un mayor potencial en aplicaciones que incluyan estructuras blandas y flexibles debido a sus estructuras biomiméticas y, especialmente, a sus excelentes propiedades mecánicas, eléctricas y sensoriales [10]. Aún así, en el campo de la robótica blanda continúan siendo los más empleados gracias a su mayor desarrollo y fiabilidad.

12 ESTADO DEL ARTE

UNIVERSIDAD POLITÉCNICA DE MADRID ESCUELA TÉCNICA SUPERIOR DE INGENIEROS INDUSTRIALES

### 2.1.2. Sensores capacitivos

En este segundo grupo se encuentran sensores empleados principalmente en robots quirúrgicos y médicos o para el modelado del comportamiento humano. También destaca su uso en aplicaciones que requieran medir presiones o fuerzas.
En la actualidad, destacan especialmente los sensores de presión basados en el uso de MXene. El uso de estos materiales bidimensionales de reciente descubrimiento está creciendo exponencialmente debido a sus excelentes propiedades eléctricas, mecánicas y químicas. Su nombre se deriva de su estructura química. La M representa el elemento de transición, generalmente titanio (Ti), vanadio (V), niobio (Nb) o tantalio (Ta), mientras que la X representa el elemento ligador, generalmente carbono (C) o nitrógeno (N) [11]. La composición de estos materiales es apreciable en la figura 2.6. Destacar que estos materiales proceden de otros denominados MAX. Los MAX, como se aprecia en la imagen, contienen varias capas del MXene al que dan lugar entre las cuales se encuentra un elemento adicional que es eliminado durante la extracción del MXene (denominado elemento grabado o A) [12].

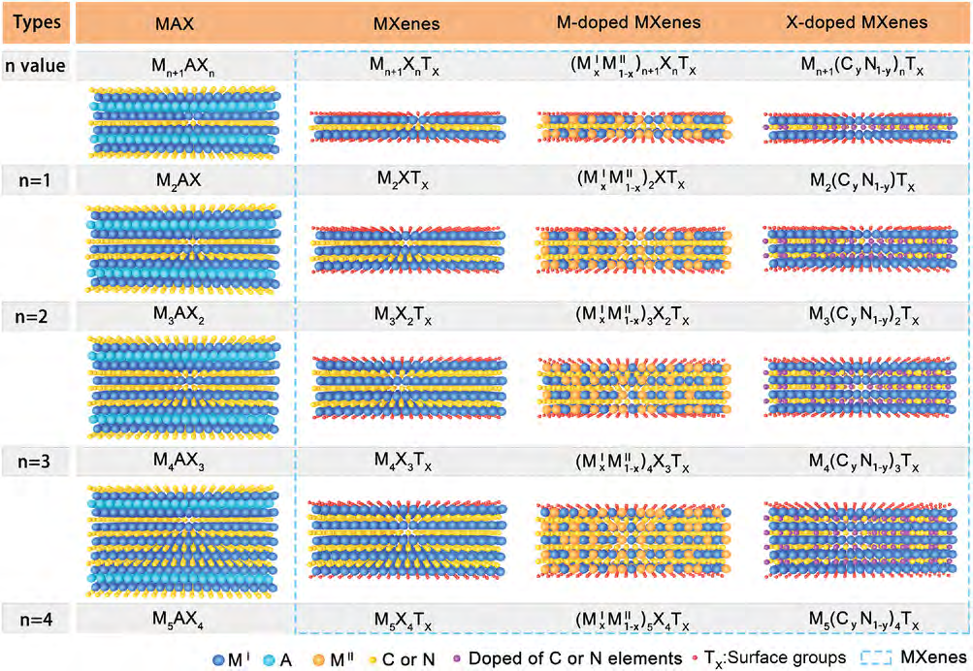
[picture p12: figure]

Figura 2.6 Estructura esquemática de los MXene, incluyendo los dopados con elementos de transición M y los dopados con elementos ligadores X, y los MAX de los que provienen. Fuente [12]

Sus aplicaciones son muy amplias: desde la industria energética hasta la industria electrónica. A pesar de ello, esta sección se centrará en sus aplicaciones como sensor de presión.
El principio de funcionamiento es similar al de un condensador, añadiendo la posibilidad de deformación del mismo. Esto se logra gracias a la adición de varias capas de un MXene una encima de otra (denominadas nanosheets), empleando como substrato para

SENSORIZACIÓN EN ROBÓTICA BLANDA 13

TRABAJO FIN DE GRADO
SENSORIZACIÓN Y CONTROL DE UN ROBOT BLANDO MANIPULADOR - RAÚL MOLINA GÓMEZ

adherir las distintas capas un dieléctrico como una silicona o un hidrogel. De esta forma, el material se comporta como varios condensadores en serie. Así, al aplicar una fuerza compresiva sobre el material se modifica la capacidad entre las distintas capas, lo que se puede emplear como medida indirecta de la presión a la que está sometido el material. Un ejemplo se puede encontrar en [13], donde se emplea una matriz salina elastomérica en conjunción con láminas del MXene T i3C32Tx, logrando así una elevada precisión en las medidas de presión realizadas, incluso para los movimientos más discretos como el de las cuerdas vocales al hablar o el latido del corazón. Todos estos resultados se puede ver en la figura 2.7.

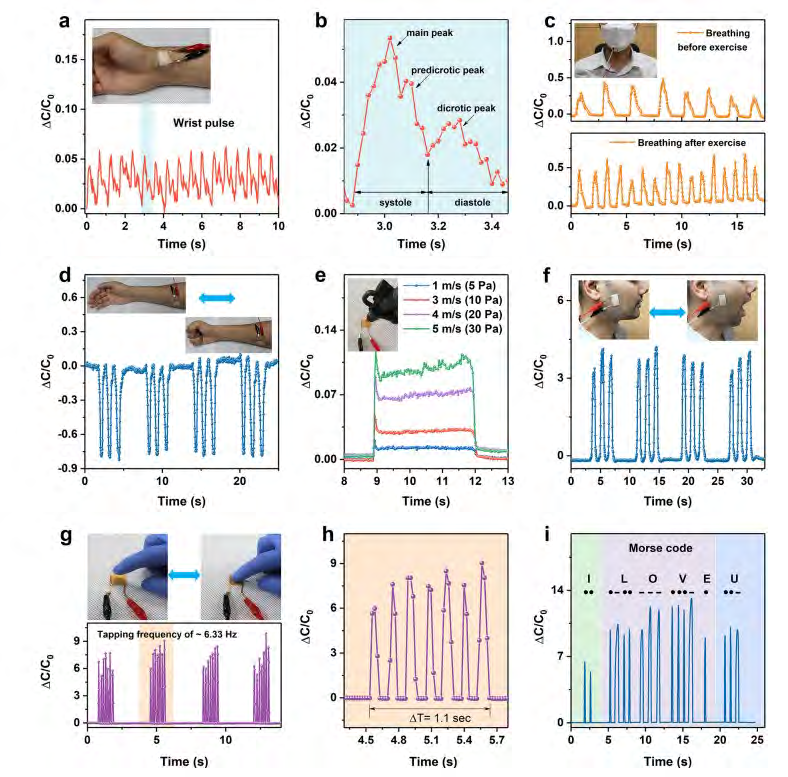
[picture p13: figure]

Figura 2.7 Resultados de un sensor capacitivo realizado con un MXene y una matriz elastomérica. Fuente [13]

También se pueden encontrar sensores piezorresistivos que emplean esta misma tecnología, empleando como substrato un material conductor y midiendo la diferencia de resistencia que presentan las capas de MXene. Un ejemplo es el trabajo realizado por Zhidong Zhang et al. [14] cuyas conclusiones se aprecian en la figura 2.8.

14 ESTADO DEL ARTE

UNIVERSIDAD POLITÉCNICA DE MADRID ESCUELA TÉCNICA SUPERIOR DE INGENIEROS INDUSTRIALES

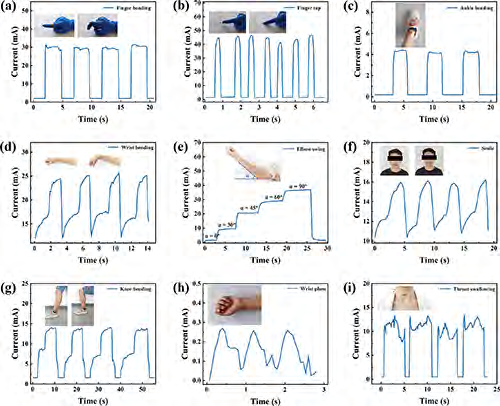
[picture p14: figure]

Figura 2.8 Resultados de un sensor flexible piezorresistivo realizado con un MXene. Fuente [14]

Asimismo se ha logrado la creación exitosa de otros sensores capacitivos, como es el caso del trabajo en [15], donde se obtiene un sensor capacitivo empleando fibras elásticas rellenas de metal líquido (la aleación eutéctica de galio e indio, conocida como EGaIn). Al deformar dicho sensor se obtiene un cambio en la capacidad del material gracias al movimiento del metal líquido en el interior de las fibras. Así, se logra una buena sensibilidad en la medida.

### 2.1.3. Sensores ópticos

Estos sensores se basan en la modificación o el movimiento de alguna propiedad visible del sensor, como la intensidad lumínica o el color, para la posterior captura de imágenes con una cámara que serán procesadas mediante un software de visión por computador para así controlar la posición y el comportamiento del Soft Robot.
Un ejemplo de este tipo de sensores lo encontramos en el trabajo realizado por Jaewoong Jung, Myungsun Park, DongWook Kim y Yong-Lae Park [16]. En él se emplea un método por el cual dependiendo de la deformación que sufra el Soft Robot se iluminará más o menos. Se basa en el uso de un emisor led y una capa reflectora. Cuando el Soft Robot está en reposo, la luz se relfeja hasta el final, mientras que conforme se deforma surgen en la capa reflectora pequeñas roturas que permiten que la luz escape, lo que reduce el rango que alcanza la luz dentro del Soft Robot. Este método se puede apreciar en la figura 2.9, junto a su resultado visual.

SENSORIZACIÓN EN ROBÓTICA BLANDA 15

TRABAJO FIN DE GRADO
SENSORIZACIÓN Y CONTROL DE UN ROBOT BLANDO MANIPULADOR - RAÚL MOLINA GÓMEZ
(a) Esquema de funcionamiento de un sensor óptico
(b) Resultado visual de la deformación producida en el Soft Robot

Figura 2.9 Ejemplo de funcionamiento de un sensor óptico empleado en robótica blanda. Fuente [16]

### 2.1.4. Sensores magnéticos

Los sensores pertenecientes a este grupo más empleados en robótica blanda se basan en el Efecto Hall. Este fenómeno físico que se da en presencia de materiales conductores y campos magnéticos (generados habitualmente por un electroimán o un imán permanente) se emplea en el ámbito de la robótica blanda para determinar la fuerza que ejerce el extremo o la presión ejercida por o sobre él.
Para el caso de la robótica blanda, estos sensores deben presentar una estructura flexible para no impedir el correcto comportamiento del Soft Robot. Es por ello que normalmente se emplea un imán embebido en algún tipo de material elastómero, como puede ser una silicona.
Un ejemplo del uso de este tipo de tecnología es el trabajo publicado por el IEEE proveniente de la Conferencia Internacional en Robótica y Automática del 2017 [17]. En él se presenta un sensor magnético de Efecto Hall con medición en los 3 ejes. Mediante el uso de un pequeño imán permanente embebido en una matriz de silicona con un sensor de Efecto Hall ubicado justo en el extremo del Soft Robot, se puede detectar la fuerza y presión ejercidas por el extremo del robot. La disposición del sensor se puede observar en la figura 2.10a, donde se aprecia el sensor de fuerza para validar los sensores de Efecto Hall, los cuales se ubican en las tres pequeñas protuberancias de silicona de los dedos del robot. Se logra así un sensor de fuerza con mediciones en los 3 ejes espaciales, detectando así tanto esfuerzos normales como cortantes con una resolución de 0.007N. Se probó en el robot Vizzy para el trabajo con humanos obteniendo resultados exitosos, como se observa en la figura 2.10b.

16 ESTADO DEL ARTE

UNIVERSIDAD POLITÉCNICA DE MADRID ESCUELA TÉCNICA SUPERIOR DE INGENIEROS INDUSTRIALES

(a) Ubicación y uso de un sensor de Efecto Hall
en un Soft Robot | (b) Resultados del uso de un sensor de Efecto Hall en un Soft Robot

Figura 2.10 Ejemplo de funcionamiento de un sensor magnético empleado en robótica blanda. Fuente [17]

### 2.1.5. Sensores inductivos

Estos sensores quizá sean los menos empleados en el campo de la robótica blanda. La principal causa de este hecho es su principio de funcionamiento, el cual se basa en el cambio de la inductancia del sensor o la inductancia mutua con otro objeto debido a la variación de la permeabilidad relativa de medio. Al emplear bobinas para la fabricación de estos sensores, los dispositivos fabricados suelen tener un tamaño excesivo o una rigidez elevada para su implementación en un Soft Robot. A pesar de ello, este tipo de sensores suele contar con ciertas ventajas, como su mayor rango dinámico o la posibilidad de obtener salidas lineales a la medida a realizar, que hacen que la investigación acerca de ellos no se detenga de forma inmediata.
Así, existen algunos trabajos de cierta relevancia que utilizan este tipo de sensores. Un ejemplo es el trabajo en [18]. En él se basan en el principio de la variación de la inductancia propia de una bobina al sufrir una deformación (similar a un muelle). Estos da lugar a una función logarítimica, como se puede apreciar en la figura 2.11a. Esta variación de inductancia se puede aprovechar para medir deformación en el material, como en la figura esquemática 2.11b. El inconveniente surgido es la necesidad de utilizar un inductor suficientemente flexible para que no impida la deformación normal del Soft Robot que tenga implementado esta tecnología.

SENSORIZACIÓN EN ROBÓTICA BLANDA 17

TRABAJO FIN DE GRADO
SENSORIZACIÓN Y CONTROL DE UN ROBOT BLANDO MANIPULADOR - RAÚL MOLINA GÓMEZ
(a) Variación de la inductancia propia de una bobina en función de la deformación que sufre

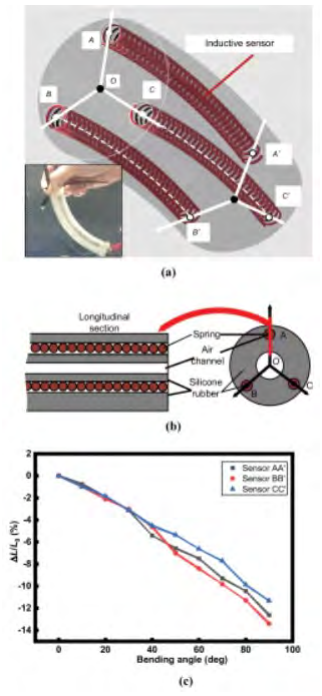
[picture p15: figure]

(b) Aplicaciones de los sensores inductivos en la robótica blanda

Figura 2.11 Ejemplo de uso y caracterización de un sensor inductivo aplicado a la robótica blanda. Fuente [18]

### 2.1.6. Sensores basados en corrientes de Foucault

Los sensores pertenecientes a este grupo no han tenido mucho recorrido en el ámbito de la robótica blanda. A pesar de ello, en los últimos años algunos grupo de investigación han ido desarrollando ciertos dispositivos que permiten mediciones de excepcional precisión mediante el uso de esta técnica. Algunos de los motivos por los que se ha comenzado a investigar acerca de estos sensores son su baja histéresis, su buena repetitibilidad, su elevada robustez ante contaminantes atmosféricos y su elevada sensibilidad. Habitualmente se emplean para mediciones de presión o fuerza [4].
En el trabajo en [19] se nos presenta una matriz de sensores (denominado Soft Inductive Tactile Sensor o SITS (figura 2.12a) que, basándose en el principio de la inducción electromagnética en materiales conductores, es capaz de cuantificar la fuerza ejercida por el Soft Robot midiendo las corrientes parásitas o de Foucault que surgen en cada uno de los sensores que la compone. De esta forma se logran resoluciones de 0.82mN en un rango que va desde los 0 a los 15N de fuerza. En el experimento mostrado en la figura 2.12b se observa la excelente detección del peso de los materiales ubicados sobre cada sensor.

18 ESTADO DEL ARTE

UNIVERSIDAD POLITÉCNICA DE MADRID ESCUELA TÉCNICA SUPERIOR DE INGENIEROS INDUSTRIALES

(a) Modelo esquemático y principio de funcionamiento del sensor SITS
(b) Comprobación de la eficacia del sensor SITS

Figura 2.12 Creación, uso y validación de un sensor basado en corrientes de Foucault. Fuente [19]

## 2.2. Métodos de modelado y control en robótica blanda

El modelado de un Soft Robot es una de las tareas más complejas a las que se enfrenta este campo. El principal motivo es la estructura flexible que presentan este tipo de robots, lo que en muchas ocasiones lleva al empleo de herramientas muy distintas a las utilizadas en el modelado de los robots rígidos tradicionales. Este hecho a su vez dificulta en gran medida el control de estos robots.
La principal característica que poseen los Soft Robots es su cuerpo blando y maleable, al no contar con elementos rígidos no existe una cadena cinemática rígida a modelar. De esta forma, un Soft Robot puede verse como una estructura continua de infinitos grados de libertad, lo que impide el uso de la gran mayoría de los métodos de modelado y control utilizados en la robótica tradicional.
Otra de las diferencias puede verse en la figura 2.13. En ella se aprecia que en la robótica blanda lo que se actúa no es lo que se controla. En otras palabras, el control de los actuadores no se hace de manera directa como en un motor, sino que es necesario controlar otra variable (como el caudal de aire en un Soft Robot neumático), que es la que “ordena” al actuador a realizar una determinada acción según el control previo.

Figura 2.13 Los dos pasos necesarios para el modelado de robots blandos: modelado específico (entre el espacio de los actuadores y el de las configuraciones) y modelado independiente (entre el espacio de configuraciones y el de la tarea). Fuente [20]

MÉTODOS DE MODELADO Y CONTROL EN ROBÓTICA BLANDA 19

TRABAJO FIN DE GRADO
SENSORIZACIÓN Y CONTROL DE UN ROBOT BLANDO MANIPULADOR - RAÚL MOLINA GÓMEZ

Con el fin de abordar con éxito el modelado y control de los Soft Robots, han surgido diversas técnicas que permiten realizar estas tareas. Estos métodos, resumidos en la figura 2.14, se pueden clasificar en tres principales grupos [21]:

En el primer grupo se incluyen todos aquellos métodos que tienen como base el modelado del comportamiento del Soft Robot mediante métodos numéricos, como pueden ser las técnicas que emplean elementos finitos. Esta metodología suele ser la más precisa para el modelado se los Soft Robots, si bien se suele aplicar cuando el problema presenta una complejidad de cálculo excesiva que impidan usar otros métodos. Un ejemplo sería el modelado del caudal introducido en las cámaras de un Soft Robot neumático.

El segundo de ellos recoge aquellos procedimientos relacionados con el modelado del robot mediante el uso de ecuaciones cinemáticas aproximadas, similares a las empleadas en la robótica tradicional. En estos casos , se hace una aproximación de los parámetros que caracterizan la deformación, como puede ser la longitud de la generatriz de un robot cilíndrico o de cables. Estos procedimientos suelen emplearse cuando la complejidad del problema no es muy elevada, o las hipótesis necesarias para su aplicación se cumplen. Un ejemplo es el modelado suponiendo curvatura constante o PCC.

El tercer grupo incluye aquella técnicas que se basan en el empleo de métodos experimentales. En este caso, y debido a la elevada complejidad que supone el modelado del comportamiento del robot, se recurre a la adquisición de datos empíricos, obtenidos mediante la realización de experimentos, que relacionan diversas características del robot entre sí, como, por ejemplo, la posición del extremo con las señales de control de los actuadores. Posteriormente, estos datos se podrán tratar de múltiples formas para obtener un modelo final del comportamiento del robot. Algunas de estas técnicas de tratamiento de los datos están relacionadas con el entrenamiento de redes neuronales.

20 ESTADO DEL ARTE

UNIVERSIDAD POLITÉCNICA DE MADRID ESCUELA TÉCNICA SUPERIOR DE INGENIEROS INDUSTRIALES

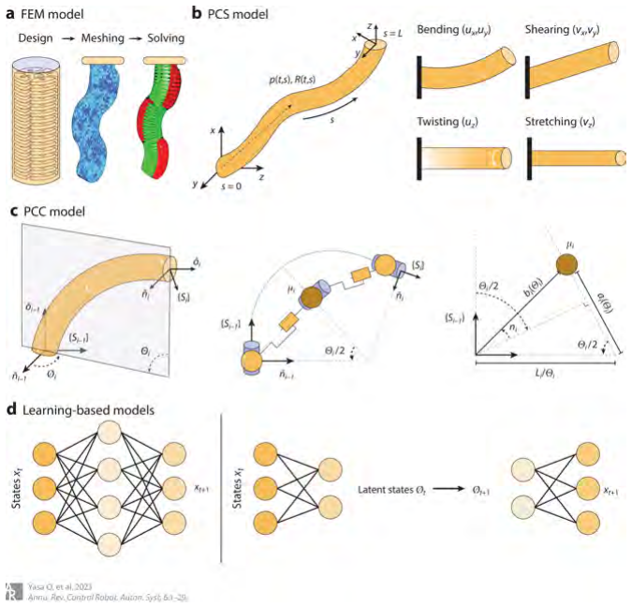
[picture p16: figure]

Figura 2.14 Principales métodos para el modelado de Soft Robots. Fuente [21]

Respecto al control de estos robots, existen métodos muy similares a los empleados en robótica tradicional. Estas técnicas se resumen en la figura 2.15 y principalmente consisten en la formulación de reguladores para controlar tanto la dinámica como la cinemática del Soft Robot conociendo los respectivos modelos del comportamiento del robot o en la extracción y el empleo de datos experimentales del movimiento del robot para posteriormente entrenar una red neuronal que permita el control del robot sin tener conocimiento explícito de su modelo.

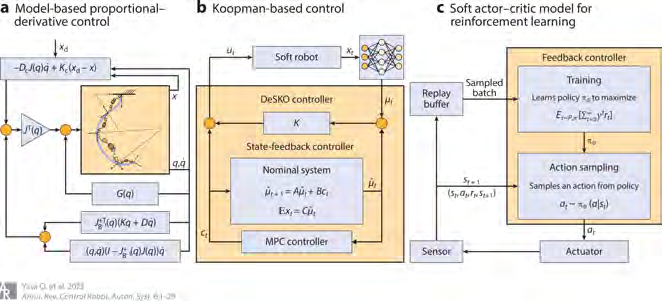
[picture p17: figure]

Figura 2.15 Principales métodos para el control de Soft Robots. Fuente [21]

A continuación, se explicarán en mayor detalle los métodos aquí nombrados para el modelado y el control de Soft Robots.

MÉTODOS DE MODELADO Y CONTROL EN ROBÓTICA BLANDA 21

TRABAJO FIN DE GRADO
SENSORIZACIÓN Y CONTROL DE UN ROBOT BLANDO MANIPULADOR - RAÚL MOLINA GÓMEZ

### 2.2.1. Métodos numéricos. Modelado mediante elementos finitos

Este tipo de técnicas consiste en la simulación por ordenador del Soft Robot a controlar para predecir el comportamiento que tendrá en la realidad. Se han desarrollado diversas herramientas para logran este objetivo, aunque destacan principalmente las que emplean elementos finitos o FEM.
El objetivo del empleo de estas herramientas, entre las que se encuentra SOFA o Simulation Open Framework Architecture de sus siglas en inglés, es modelar el comportamiento del robot ante los estímulos de actuación, obteniendo así un modelo similar al cinemático directo e inverso. De esta forma, mediante la correcta caracterización del robot es posible conocer la deformación que debe sufrir y su correspondiente forma de actuación para lograr la posición deseada.
Un ejemplo de esta metodología se encuentra en el trabajo realizado en [22], donde medinte el empleo de un modelo no lineal en SOFA y la técnica FEM aquí descrita se logra posicionar un robot neumático de tres segmentos con errores de alrededor de 2.5 cm en cadena cerrada. En la figura 2.16 se puede ver el robot empleado, su modelado en elementos finitos en reposo y su modelado con control en tiempo real.

Figura 2.16 Modelado y control mediante elementos finitos. Fuente [22]

### 2.2.2. Métodos analíticos

Modelado basado en curvatura constante - PCC

El principal de estos métodos analíticos consiste en considerar al Soft Robot como un robot continuo compuesto por varios segmentos que al actuarse presentan una curvatura constante en su deformación (figura 2.17a). Esta hipótesis permite simplificar en gran medida la forma de obtención de una matriz de transformación homogénea desde el extremo hasta la base de cada uno de los segmentos que componen el robot, pues es posible transformar dicho Soft Robot en un equivalente modular rígido con los suficientes grados de libertad. De esta forma, se pueden emplear las mismas herramientas que se empleaban en la robótica tradicional para el modelado de los robots, obteniendo una relación entre los parámetros característicos de la curvatura con las longitudes de los segmentos, obteniendo

22 ESTADO DEL ARTE

UNIVERSIDAD POLITÉCNICA DE MADRID ESCUELA TÉCNICA SUPERIOR DE INGENIEROS INDUSTRIALES

tanto posición como orientación del extremo del segmento y, por lo tanto, del robot. Esta transformación de blando a rígido se puede observar en la figura 2.17b, proveniente del trabajo realizado en [23].

(a) Esquema cinemático
de un robot con curvatura constante

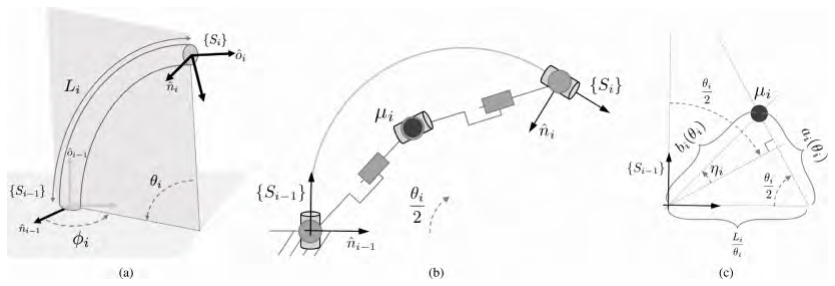
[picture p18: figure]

(b) Modelo rígido equivalente

Figura 2.17 Modelado basado en curvatura constante. Fuente [23]

Modelado basado en la teoría de vigas de Cosserat, Cosserat rod model o PCS

Además de los modelos basados en curvatura constante existen también otros intentos de modelar el comportamiento de los Soft Robots. Un ejemplo es el uso de la teoría de vigas de Cosserat, conocida también como deformación constante por segmentos o PCS por sus siglas en inglés piecewise constant strain. Este modelo aproxima la estructura blanda del Soft Robot a varios segmentos cilíndricos largos, similares a una viga. De esta forma, al conocer las simetrías entre segmentos siguiendo esta hipótesis, se simplifica la mecánica continua de cada uno de ellos considerando exclusivamente los esfuerzos de flexión, torsión, cizalladura y alargamiento a los que están sometidos cuando se actúa el robot (figura 2.18). Esta hipótesis es especialmente útil es robots blandos con morfologías modulares, al igual que en el caso del PCC. Un ejemplo del uso de esta metodología se encuentra en el trabajo realizado en [24], donde se desarrollan las ecuaciones necesarias para modelar un Soft Robot actuado mediante tendones flexibles, como se observa en la figura 2.18.

MÉTODOS DE MODELADO Y CONTROL EN ROBÓTICA BLANDA 23

TRABAJO FIN DE GRADO
SENSORIZACIÓN Y CONTROL DE UN ROBOT BLANDO MANIPULADOR - RAÚL MOLINA GÓMEZ

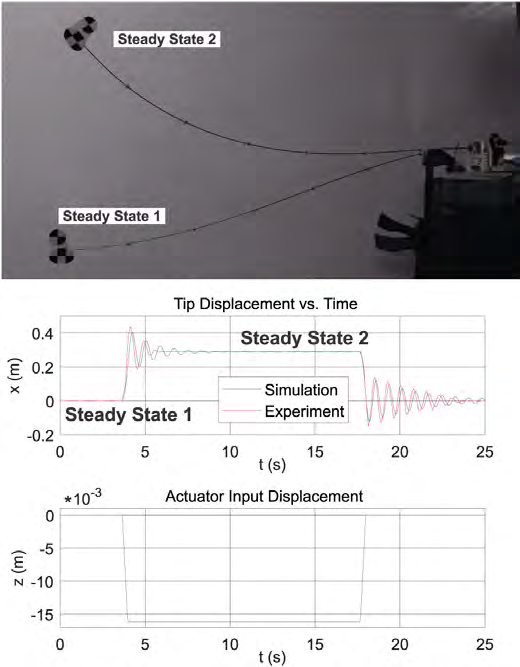
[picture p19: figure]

Figura 2.18 Control de un Soft Robot actuado con tendones mediante el uso de la teoría de vigas de Cosserat. Fuente [24]

Otros modelos analíticos utilizados en robótica blanda

Además de los modelos mencionados anteriormente, existen otros que emplean distintas técnicas más complejas para lograr resultados de mayor precisión en robots que no se adaptan bien a los modelos más utilizados, como el PCC o el PCS. Algunos de estos diferentes acercamientos al problema del modelado de Soft Robots se encuentran en los trabajos realizados en [25] y [26].
En el primero, se formula un modelo a partir del uso de la curvatura polinómica (ecuación 2.2), que es una aproximación finita de la ecuación 2.1, que define la curvatura del robot en un determinado instante de tiempo para una posición dada. En este sentido, para un grado de aproximación m = 0, el modelo propuesto es el mismo que en el caso del PCC, pues sería curvatura constante.

q(s, t) = X∞

i=0

Θi(t)s

i
(2.1)

q(s, t) ≃

Xm

i=0

Θi(t)s

i
(2.2)

24 ESTADO DEL ARTE

UNIVERSIDAD POLITÉCNICA DE MADRID ESCUELA TÉCNICA SUPERIOR DE INGENIEROS INDUSTRIALES

De esta forma, se desarrollan las ecuaciones necesarias para el modelado dinámico y cinemático empleando un regulador PD basado en el uso de esta curvatura polinómica, denominado PD-poly, que permite al robot alcanzar las posiciones correctamente gracias a la mejor aproximación de su forma así como a la consideración del peso y el resto de factores que afectan a su dinámica, como las fuerzas centrífugas y de coriolis o la propia inercia del robot. Los resultados se observan en la figura 2.19, donde se compara el torque y las posiciones en coordenadas modulares y en el espacio cartesiano.

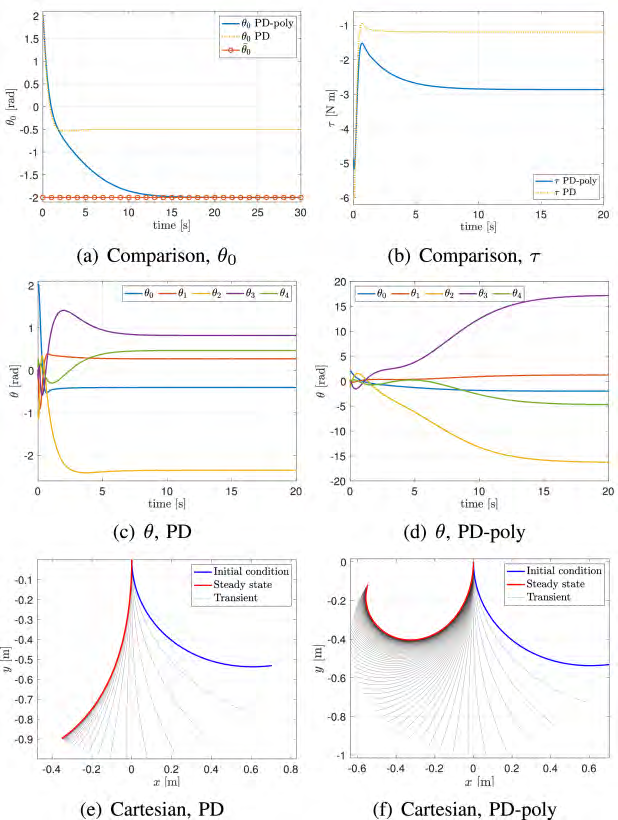
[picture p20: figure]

Figura 2.19 Resultados de una simulación realizada para un robot blando manipulador utilizando un modelo basado en la curvatura polinómica de 4º grado. Fuente [25]

En el segundo, se emplean Curvas Hodógrafas Pitagóricas; un tipo especial de curvas paramétricas que tienen la propiedad de que tanto la magnitud como la dirección de su vector velocidad son funciones cuadráticas de su parámetro. Mediante el uso de estas curvas paramétricas, se logra unos modelos cinemáticos directo e inverso que aplicados en el robot RobotinoXT se logran errores de unos 2 mm de media.

MÉTODOS DE MODELADO Y CONTROL EN ROBÓTICA BLANDA 25

TRABAJO FIN DE GRADO
SENSORIZACIÓN Y CONTROL DE UN ROBOT BLANDO MANIPULADOR - RAÚL MOLINA GÓMEZ

### 2.2.3. Métodos experimentales. Métodos basados en el entrena-

miento de redes neuronales

Por último, se encuentran las técnicas experimentales. Esta metodología de control de Soft Robots ha tenido una expansión significativa en los últimos años debido al auge de las tecnologías que hacen uso de la Inteligencia Artificial. Su principio de uso es la extracción y manipulación de datos obtenidos mediante la realización de experimentos que emplean directamente al robot físico sin previa simulación para posteriormente entrenar una red neuronal o procesarlos mediante otras técnicas de Deep Learning, como el aprendizaje por refuerzo (Reinforcement Learning).
La ventaja que presentan estos métodos con respecto a los anteriores es que para abordar con éxito el control no es necesaria la caracterización del comportamiento del robot y, por lo tanto, no se requiere un modelo del mismo. Esto supone una gran ventaja, pues la obtención de modelos en robótica blanda como se ha visto son tareas de muy elevada complejidad que en muchos casos solo se logran mediante hipótesis que aproximan los comportamientos de los robots, perdiéndose así precisión en los resultados deseados. Es por ello que en la actualidad son estas las técnicas más empleadas para el control de los Soft Robots.
Un ejemplo de lo aquí expuesto se encuentra en el trabajo realizado por Gabor Soter et al. [27], donde mediante el entrenamiento de una red neuronal y un autoencoder convolucional se logra que un tentáculo blando conozca su forma y posición a partir de la medida de unos sensores contenidos en su interior. Los resultados obtenidos se pueden ver en la figura 2.20.

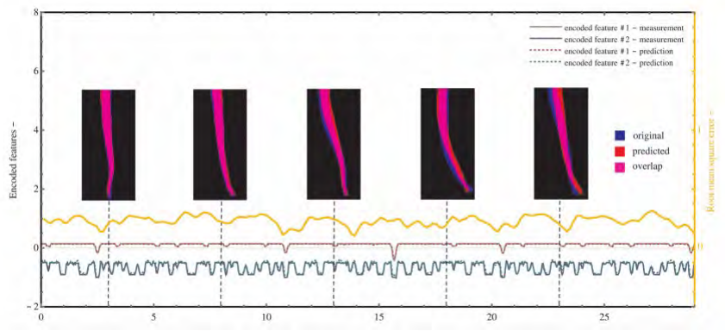
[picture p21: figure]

Figura 2.20 Resultados del empleo de una red neuronal para conocer la posición de un robot blando a partir de las medidas de sus sensores de deformación. Fuente [27]

26 ESTADO DEL ARTE

UNIVERSIDAD POLITÉCNICA DE MADRID ESCUELA TÉCNICA SUPERIOR DE INGENIEROS INDUSTRIALES

Finalmente, cabe destacar el empleo de otras técnicas que incluyen Machine Learning, como es el caso de los robots entrenados mediante aprendizaje por refuerzo. En estos casos, se parte de un modelo aproximado, como puede ser el PCC, y a partir de él se ajusta el comportamiento real del robot mediante la toma de datos con las que se entrena una red neuronal de corrección. Un ejemplo se da en [28], donde mediante el uso de esta técnica y partiendo de las ecuaciones del PCC se logra el control en posición de un robot blando manipulador, logrando errores en el seguimiento de las trayectorias de en torno a 1 cm sin carga y a 2 cm con carga. El robot a controlar se aprecia en la figura 2.21.

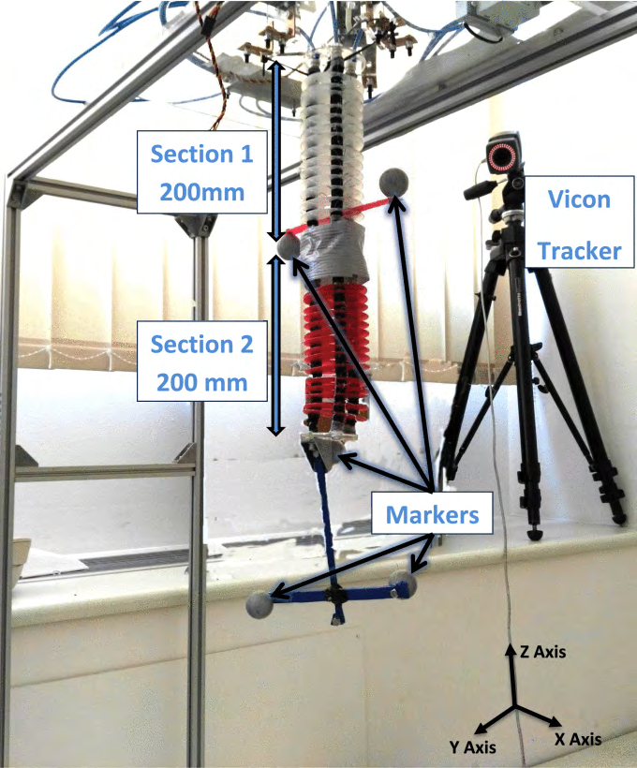
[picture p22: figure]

Figura 2.21 Robot blando y su setup para el control con el uso de PCC y aprendizaje por refuerzo. Fuente [28]

MÉTODOS DE MODELADO Y CONTROL EN ROBÓTICA BLANDA 27

Capítulo3

# Estudio y caracterización de los

# sensores

En robótica, la correcta selección de los sensores es de vital importancia para poder abordar con éxito el control del robot para los que están destinados. En el caso de la robótica blanda esta problemática se acentúa debido a las restricciones presentadas en la sección 2.1, con lo que se debe hacer especial hincapié en la búsqueda de sensores que cumplan con las características necesarias para que el Soft Robot se mueva de forma adecuada mientras que permita mediciones con una elevada resolución para lograr resultados precisos en el movimiento posterior al control del robot.
Durante este proyecto, y debido a lo comentado con anterioridad, la parte que aquí se aborda adquirió especial relevancia, pues todo lo aquí realizado afectaba al resto de partes del trabajo. Es por este motivo que se procedió a analizar las características que debían presentar los sensores y su comportamiento final para el correcto planteamiento de los métodos de control del robot aquí mostrado. Asimismo, se ideó un sistema de medida de los sensores que lograra la máxima resolución y precisión posible.
En este capítulo se presentan las distintas fases que componen la parte de sensorización de este proyecto, desde la selección y compra de los dispositivos hasta la caracterización y prueba de los mismos.

## 3.1. Selección de los sensores

Para este proyecto, además de las restricciones mencionadas anteriormente, se han impuesto otras debido a la naturaleza elástica del material y a las restricciones de alcance y temporalidad del trabajo. Esto último es el principal motivo que explica la imposibilidad de fabricación de un sensor propio, como suele ser la principal técnica de sensorización en robótica blanda (sección 2.1). También cabe destacar que los sensores ópticos como

29

TRABAJO FIN DE GRADO
SENSORIZACIÓN Y CONTROL DE UN ROBOT BLANDO MANIPULADOR - RAÚL MOLINA GÓMEZ

cámaras o web-cams quedaban descartados debido a que el objetivo de este proyecto es controlar un robot de forma autónoma sin depender del exterior. Es por ello que la única posibilidad era la de encontrar un sensor comercial de bajo coste con la mayor calidad de medición posible que cumpliera con todos los requisitos para abordar de manera correcta el problema del control de este Soft Robot.
Debido a la escasez de sensores elásticos para robótica blanda en el mercado, la elección se pudo realizar de forma sencilla y rápida. La decisión final fue un sensor resistivo elastómero de la empresa Adafruit [2] (Figura 3.1). Las razones en la que se basa esta decisión son:

Facilidad de medición: Al ser un sensor resistivo, como los vistos en la sección 2.1.1, cuyo funcionamiento se basa en la variación de su resistividad ente una deformación, en este caso, de tipo longitudinal, permite buenas mediciones con una instrumentación sencilla.

Material de fabricación: Este sensor está compuesto de negro carbón en una matriz de goma. Esto le aporta una excelente durabilidad y flexibilidad además de facilitar su manejo, pues no es un material tóxico ni que se vea afectado por campos electromagnéticos que puedan modificar los valores medidos debido a interferencias con el exterior.

Diseño del Soft Robot: Debido a la forma y diseño de los segmentos que componen a PAUL, estos sensores eran los más óptimos en cuanto a facilidad de incorporación. Esto se debe a que en el anterior trabajo [1] donde se abordó el problema del diseño, se implementaron unos canales pensados para sensores de este tipo, con lo que la incorporación de estos sensores al diseño era inmediata.

Coste del sensor: La última gran ventaja que presentaban estos sensores era su relativamente bajo coste (9.95 e/m), con lo que se reducía en gran medida el pre-

supuesto al adquirir varios metros de este sensor. A esto se suma la fiabilidad de los productos de la empresa Adafruit y su rápido envío.

Figura 3.1 Sensor resistivo elastómero empleado en el control en cadena cerrada de PAUL. Fuente [2]

30 ESTUDIO Y CARACTERIZACIÓN DE LOS SENSORES

UNIVERSIDAD POLITÉCNICA DE MADRID ESCUELA TÉCNICA SUPERIOR DE INGENIEROS INDUSTRIALES

Aún así, se observó que estos sensores presentaban a su vez tres grandes inconvenientes. El primero estaba relacionado con el rango de medición, pues este era excesivamente pequeño para las deformaciones a las que estaría sometido el sensor y se saturaba la medida con rapidez. El segundo de ellos era la elevada histéresis en la resistividad del material, pues una vez deformado y posteriormente liberado de este esfuerzo normal tardaba de 1 a 2 minutos en regresar a su punto de equilibrio. La tercera desventaja se relacionaba con la baja resolución que ofrecía el sensor comercial.
Los dos primeros problemas asociados a este sensor se solucionaron debido a un cambio de comportamiento en los sensores y el tercero de ellos se solventó gracias al uso de hardware de medición. Todos estos problemas y su respectiva solución se explicarán con mayor detalle en secciones posteriores.

## 3.2. Método de medición

Tras la selección y la adquisición de los sensores, el siguiente objetivo era establecer el método de medición de las variaciones de resistencia que presentaban los sensores ante la deformación longitudinal. Dado que la resistencia se relaciona con tensión e intensidad mediante la Ley de Ohm (V = R · I) se ofrecían tres posibilidades: o medir resistencia, o medir tensión o medir intensidad.
La primera de ellas implica medir tanto una tensión como una intensidad, pues no hay dispositivo de medida capaz de obtener de manera “directa” la resistencia que presenta un objeto. Es por ello que nos centraremos en las ventajas e inconvenientes de la medición de tensiones o intensidades.
En el caso de la medida de una corriente, es necesario un dispositivo que o bien detecte intensidades muy pequeñas o bien que mida corrientes más elevadas. En el primero de los casos, el dispositivo de medida tendría un coste muy elevado, pues requiere de resoluciones incluso de microamperios, aunque el consumo energético sería muy bajo. El segundo supone un menor precio al no necesitar de tecnología tan avanzada a cambio de un gran consumo de energía. Además, dependiendo de la resistencia a medir será necesario un voltaje menor o mayor.
En el caso que aquí se estudia, la segunda opción sería inviable, pues el sensor inicialmente se encuentra en un rango de varios kilohmnios, con lo que la tensión a aplicar debería ser muy elevada (de varios cientos de voltios), con lo que la potencia y el calor disipados serían excesivamente altos y podría dañar la instrumentación electrónica, el sensor o incluso el propio robot. Esto implica que si se quiere implementar un método de medición basado en medidas de corriente, se ha de adquirir un hardware con la suficiente sensibilidad que, para este proyecto, se encontraba en las decenas de microamperios (suponiendo fuentes de tensión comerciales de en torno a los 30V).

MÉTODO DE MEDICIÓN 31

TRABAJO FIN DE GRADO
SENSORIZACIÓN Y CONTROL DE UN ROBOT BLANDO MANIPULADOR - RAÚL MOLINA GÓMEZ

En cambio, en el caso de la medida de tensiones, la sensibilidad de la medida no supone un problema en sí mismo, pues mientras el dispositivo de medida reciba una señal clara con suficiente energía se puede realizar una medida de forma sencilla. A esto se une la facilidad de lectura de los datos, pues se encuentra en decenas de voltios y no es necesario escalar la medida con el uso de amplificadores. Es debido a estas ventajas con respecto a la medición de corriente que se decidió emplear este método.
Para poder aplicar esta técnica de medición era necesario emplear un divisor de tensión o un puente de resistencias, pues de otra manera siempre se mediría el mismo valor de tensión, al ser completamente independiente de la resistencia si está siendo aplicado por una fuente de tensión constante. Así, mediante un divisor de tensión adecuado se logra que al variar una de las resistencias (en este caso el sensor) y mientras la otra se mantenga siempre fija se mida de manera indirecta los cambios de resistencia en el sensor y, con ello, la deformación que está sufriendo.

### 3.2.1. Hardware de medición

Una vez seleccionada la técnica de medición de las deformaciones del Soft Robot el siguiente paso a completar es elegir el hardware que capture los datos medidos para posteriormente procesarlos de manera adecuada. En el anterior trabajo realizado sobre este mismo robot ya se empleaba un microcontrolador Arduino Due (figura 3.2) que permitía generar las señales de control necesarias para abrir o cerrar las válvulas en función de la acción que se desease realizar. Es por ello que el hardware de captura de datos que se empleó fue este mismo Arduino Due.

Figura 3.2 Microcontrolador Arduino Due empleado. Fuente: elaboración propia

Con esta decisión se abrían otras dos posibilidades: una captura directa de los datos mediante uno de los puertos con convertidor analógico-digital (ADC) y con ello medir tensiones o utilizar un hardware específico que mediante puerto serie se comunique con el microcontrolador enviando los datos ya convertidos a señales digitales para que sean procesados con posterioridad por el Arduino Due empleado.

32 ESTUDIO Y CARACTERIZACIÓN DE LOS SENSORES

UNIVERSIDAD POLITÉCNICA DE MADRID ESCUELA TÉCNICA SUPERIOR DE INGENIEROS INDUSTRIALES

La medida directa es más sencilla ya que emplea un hardware específico implementado en el microcontrolador, con lo que la comunicación y captura de los datos es inmediata. Sin embargo, presenta algunos inconvenientes:

El primero de ellos es la resolución que ofrece el Arduino Due en sus pines analógicos, pues el valor nominal de esta es de 10 bits ampliables a un máximo de 12 bits mediante comandos software. Esto supone una limitación a la hora de medir variaciones de deformación longitudinal en los sensores.

El segundo inconveniente que presenta esta técnica es el reducido rango de medida que ofrece, pues el máximo voltaje a aplicar en los pines analógicos es de 3.3V. Este hecho adquiere gran relevancia cuando la tensión a aplicar nunca es la máxima, como sucede en este caso al emplear un divisor de tensión. Esto limita enormemente las tensiones a emplear, lo que afecta a su vez a la resolución de la medida, pues la diferencia entre dos valores de voltaje medidos para una misma variación de longitud en el sensor es mucho menor ( ³,3V
2

10 = 0,0032V frente, por ejemplo, al uso de una fuente de 12V: 12V
2

10 = 0,0117V ).

El tercer gran problema, que es a su vez el de mayor importancia, es el ruido que se puede producir en la medida. Al no poseer un filtro previo a la medida y estar el sistema expuesto a las señales electromagnéticas del exterior, la precisión de la medida se puede ver comprometida, como se puede ver en las medidas de la figura 3.3 con y sin filtrado de la señal.

(a) Medida de la señal sin filtrar
(b) Medida de la señal filtrada

Figura 3.3 Ruido de la señal medida y su solución por filtrado. Fuente: elaboración propia

Son estas tres razones las que decantaron la balanza en favor del uso de un hardware de medida externo al microcontrolador. Este debía solventar estos problemas, con lo que se fijaron tres requisitos:

1. Tener un valor máximo de medida superior a 12V y, preferiblemente, a 24V, pues estos son los valores de tensión que puede ofrecer una fuente para ordenador. El motivo de emplear una fuente de tensión para ordenadores es que ya se contaba con una en el laboratorio donde se realizó este proyecto.

MÉTODO DE MEDICIÓN 33

TRABAJO FIN DE GRADO
SENSORIZACIÓN Y CONTROL DE UN ROBOT BLANDO MANIPULADOR - RAÚL MOLINA GÓMEZ
2. Tener una resolución mayor o igual a la ofrecida por el microcontrolador, pues sino no supondría una ventaja con respecto al primero.
3. Tener un comportamiento de filtro paso alto con el fin de eliminar las frecuencias provenientes del ruido exterior. Además, no debe amplificar la señal medida, pues los valores de tensión de alimentación ya se encontrarían en el rango de medida del dispositivo. Esto implica una ganancia a la salida de 0dB.

En conjunción a estos requisitos hay que añadir las características de comunicación serie del Arduino Due. Dado que ya se venían empleando 2 puertos UART, se abría la posibilidad de una comunicación de este tipo (pues el máximo de puertos UART existente en la placa Arduino Due es de cuatro), una con protocolo I2C o una de tipo SPI. Atendiendo a todos estos requisitos, los INAs o Amplificadores de Instrumentación suponen una gran opción, pues son circuitos especializados diseñados para medir pequeñas diferencias de voltaje con alta precisión. Asimismo, se abrían tres posibles opciones de compra que cumplieran las características mencionadas anteriormente: INA219 (con dos versiones A y B, se comparará la versión B por ser ligeramente mejor a la A), INA226 e INA3221. Todos estos dispositivos se pueden ver en las figuras 3.4a, 3.4b y 3.4d, respectivamente. En la tabla comparativa 3.1 se aprecian las diferencias entre los tres dispositivos. Todos los datos se han obtenido de sus respectivas datasheets ofrecidas por Texas Instruments [29], [30] y [31], respectivamente.

Dispositivo | Rango de medida (V) | Tensión de alimentación (V) | Input Offset (max) | Error en la ganacia | Corriente de reposo (max)
INA219 | 0 - 26 | 3 - 5.5 | 100 µV | 0.3 % | 1 mA
INA226 | 0 - 36 | 2.7 - 5.5 | 10 µV | 0.1 % | 0.42 mA
INA3221 | 0 - 26 | 2.7 - 5.5 | 80 µV | 0.25 % | 0.35 mA
Dispositivo | CMRR (min) | Error de medida de tensión (max) | Resolución | Número de canales | Número de direcciones I2C
INA219 | 100 dB | 0.8 % | 12 bits | 1 | 16
INA226 | 126 dB | 0.2 % | 16 bits | 1 | 16
INA3221 | 110 dB | 0.5 % | 13 bits | 3 | 4

Tabla 3.1 Tabla comparativa de las distintas características del INA219, el INA226 y el INA3221. Fuente: Elaboración propia

Mencionar que los tres dispositivos se comunican con protocolo I2C y presentan ganancia unitaria. A su vez, los tres cuentan con un muy buen rechazo al ruido, medido indirectamente mediante el CMRR (a más alto el valor, mejor rechazo del ruido). Importante señalar que todos estos dispositivos poseen un diagrama de Bode muy similar, con una frecuencia de corte superior de en torno a los 300Hz. Dado que la medida es una constante (0Hz) son más que aptos para rechazar el ruido exterior. Además, como se puede observar en la tabla 3.1, todas ellas poseen más de 9 direcciones I2C configurables (en el caso del INA3221 al contar con 3 canales por dispositivo solo son necesarios un mínimo de 3 direcciones diferentes, pues 3 · 3 = 9), lo que permite que se puedan emplear todos estos dispositivos para los tres segmentos del robot y sus nueve grados de libertad

34 ESTUDIO Y CARACTERIZACIÓN DE LOS SENSORES

UNIVERSIDAD POLITÉCNICA DE MADRID ESCUELA TÉCNICA SUPERIOR DE INGENIEROS INDUSTRIALES

totales. Destacar además que estas direcciones se programan mediante la unión por soldadura blanda de dos conectores a modo de jumpers, como se observan en las figura 3.4. Posteriormente han de programarse además por software.

(a) INA219
(b) Parte frontal del INA226 | (c) Parte trasera del INA226
(d) Parte frontal del INA3221 | (e) Parte trasera del INA3221

Figura 3.4 Selección del hardware de medición. Fuente [29], [30] y [31]

Cabe destacar especialmente el hecho de que solo es necesaria una INA3221 por segmento, pues es capaz de medir tres canales gracias a un multiplexor incorporado en su interior, lo que reduce significativamente el presupuesto y la complejidad de diseño y manejo de la instrumentación final. Además, gracias a esto el hecho de contar solo con 4 direcciones programables de I2C no supone un problema a priori, pues se usarán como máximo 3 segmentos. Así, a pesar de su menor resolución, precisión y rango en comparación con el INA226, se decidió finalmente adquirir el INA3221, pues los valores en las propiedades de la medida ofrecidos cumplían sobradamente todos los requisitos mencionados con anterioridad para la aplicación en los que se iban a emplear estos dispositivos.

MÉTODO DE MEDICIÓN 35

TRABAJO FIN DE GRADO
SENSORIZACIÓN Y CONTROL DE UN ROBOT BLANDO MANIPULADOR - RAÚL MOLINA GÓMEZ

## 3.3. Caracterización del comportamiento de los senso-

## res

Tras la adquisición y compra de los dispositivos mencionados con anterioridad, era necesario comprobar el correcto funcionamiento de dicho hardware electrónico junto al sensor para posteriormente poder caracterizar su comportamiento con éxito. Es durante este proceso donde ocurre un fenómeno inesperado y fortuito que llevará a uno de los mayores logros durante este proyecto. Es gracias a este suceso que se solucionaron todos los problemas derivados de la falta de rango y la elevada histéresis de los sensores, lo que permitió un funcionamiento mucho mejor de lo esperado inicialmente. A continuación se introduce y explica el fenómeno del cambio en el comportamiento de los sensores.

### 3.3.1. Cambio de comportamiento de los sensores

Este evento surge como consecuencia de la comprobación del correcto funcionamiento del INA3221 junto al sensor elastómero. Como parte de este proceso de verificación se procedió a montar los sensores (sin ningún tipo de adhesivo ni fijador) en uno de los segmentos del robot con el objetivo de comprobar el rango en el que se encontraban las medidas de dicho sensor y si era suficientemente amplio para el correcto funcionamiento del Soft Robot en el campo de trabajo objetivo. De esta forma, tras la debida comprobación de la que se obtuvieron unos resultados negativos, pues el sensor se saturaba mucho antes de lo esperado al igual que su histéresis suponía un grave problema; se dejaron dichos sensores montados en contacto con la silicona curada de la que está fabricado cada segmento (TinSil 8015). Cabe destacar además que para este experimento se empleó un divisor de tensión con una resistencia fija de 1kΩ, pues el rango de variación de la resistencia del sensor estaba entre los 2 y los 6kΩ, aproximadamente.
Tras esto y al cabo de una semana se procedió a examinar de nuevo el comportamiento de los sensores para idear una forma de solucionar los problemas observados en la semana anterior. Al proceder con esta nueva prueba se apreciaron pequeñas incrustaciones de silicona en los puntos de mayor contacto con el sensor. Inicialmente, no se dio excesiva importancia a este hecho, hasta que al volver a realizar la medición correspondiente el valor mostrado no se correspondía con lo obtenidos anteriormente. Es más, no solo eran diferentes, sino que además la medición era nula (señala que se incialmente se medía la caída de tensión en la resistencia fija). Dado que la tensión medida era de 0V, se concluyó que el sensor se había roto y se había generado un circuito abierto.
Como la conclusión no era lógica, pues nada podía haber producido la rotura del sensor, se procedió a examinar si el material presentaba alguna grieta no detectada anteriormente y, para facilitar esto, se estiró el sensor para poder comprobar si se había producido una sección en algún lugar. Fue aquí donde se pudo apreciar la verdad de lo que había ocurrido,

36 ESTUDIO Y CARACTERIZACIÓN DE LOS SENSORES

UNIVERSIDAD POLITÉCNICA DE MADRID ESCUELA TÉCNICA SUPERIOR DE INGENIEROS INDUSTRIALES

pues al estirar sin haberlo desconectado del dispositivo de medida se observó como los valores medidos ya no eran nulos, sino que eran positivos e iban aumentando conforme se estiraba el sensor.

Con posteriores pruebas y experimentos se pudo extraer conclusiones más certeras del nuevo comportamiento del sensor. Las principales diferencias son cuatro: rango de la medida, rango de la deformación hasta la saturación, histéresis del material y comportamiento ante la deformación.

Con respecto al rango de la medida, el nuevo sensor presenta un comportamiento muy diferente. Mientras el sensor comercial presenta un rango de medida de entre 2 a 6kΩ el sensor modificado se mueve entre los 100kΩ hasta las decenas de MΩ. Este rango varía entre los distintos sensores, dependiendo de su longitud y tiempo de contacto con la silicona del segmento, aunque siempre se encuentra entre los mismos órdenes de magnitud. Cabe destacar además que el incremento de resistencia tiende a un valor constante, por lo que para tiempos de contactos superiores a los 5 días aproximadamente no se observan variaciones significativas en estos valores de resistencia.

En lo referente al rango de la deformación, el material ahora presenta una muy superior capacidad de estiramiento previa a la saturación de la medida de resistencia del sensor. En algunos casos llega a ser de hasta 4 veces superior, como se aprecia en la figura
3.6. Esto soluciona el problema que existía relacionado con este hecho, pues gracias a esto el sensor puede detectar sin saturarse las deformaciones que pueda sufrir cada segmento en el campo de trabajo objetivo.

En cuanto a la histéresis del material, esta se vió eliminada por completo. Tras la modificación de sus propiedades, el sensor no presenta histéresis alguna, pues regresa a su estado de equilibrio casi de forma inmediata tras la liberación del esfuerzo normal aplicado. De esta forma, se soluciona otro de los inconvenientes que mostraba este sensor, pues no es necesario esperar para que se estabilice la medida y se puede actuar el robot de forma inmediata y continuada. En la figura 3.6 se aprecia este cambio.

Por último, el comportamiento ante la deformación también es significativamente distinto. En el sensor comercial se observaba un aumento exponencial de resistencia al sufrir un estiramiento (lo cual es lógico, ya que aumenta la distancia entre las partículas conductoras de negro carbón y además se disminuye la sección, con lo que la resistencia aumentaría según la ecuación R = ρ ·

L
S

), mientras que en el sensor modificado la resistencia parte de las decenas de megaohmnios y cae de forma mayoritariamente lineal hasta alcanzar la saturación. Este hecho no guarda lógica aparente, pero puede facilitar el tratamiento de las medidas dependiendo del punto de trabajo del sensor (en la zona lineal se hace más sencillo operar). Sí es han dado casos de este tipo de fenómenos anteriormente, como el trabajos realizados en [32] y en [33], como se ve en la figura 3.5, aunque no se trataban de sensores blando como en este caso, sino que se emplearon fibras de carbono.

CARACTERIZACIÓN DEL COMPORTAMIENTO DE LOS SENSORES 37

TRABAJO FIN DE GRADO
SENSORIZACIÓN Y CONTROL DE UN ROBOT BLANDO MANIPULADOR - RAÚL MOLINA GÓMEZ

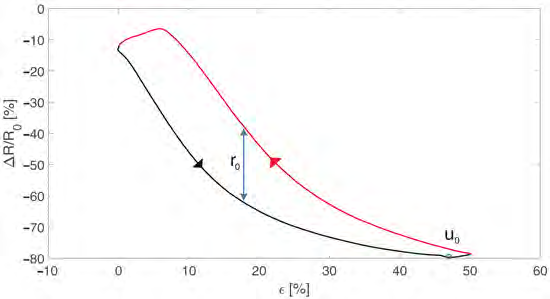
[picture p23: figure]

Figura 3.5 Comportamiento de un sensor similar al empleado en este proyecto. Fuente [32]

Todas estas diferencias son observables en la figura 3.6, donde se compara a la izquierda el comportamiento del sensor comercial ante la elongación y a la derecha el comporta-

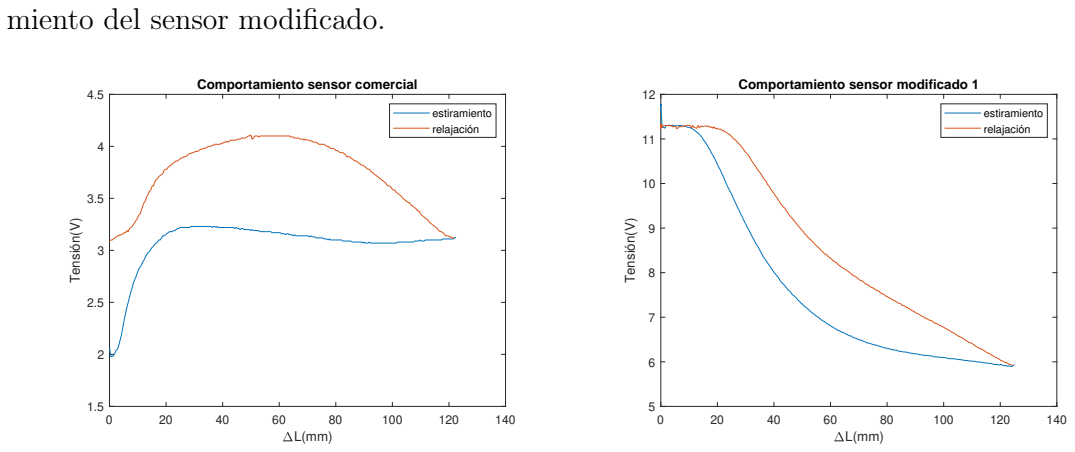
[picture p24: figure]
miento del sensor modificado.; Tensión(V); Comportamiento sensor comercial; estiramiento; relajación; Comportamiento sensor modificado 1

(a) Comportamiento del sensor comercial al variar su longitud
(b) Comportamiento de un sensor modificado al variar su longitud

Figura 3.6 Comparación del comportamiento de los sensores comercial y modificado. Fuente: elaboración propia

Como se puede ver, la diferencia entre ambos comportamientos es muy significativa, especialmente en el retorno al estado de reposo.
Cabe señalar además que a día de hoy no ha sido posible encontrar una explicación para este fenómeno, pues no es lógico su funcionamiento. Una hipótesis inicial podría ser que se haya producido una reacción química entre los materiales que conforman el sensor y la silicona curada con la que se moldean los segmentos de PAUL, ya que cualquier otra explicación no parece físicamente probable. Para verificar esta hipótesis sería necesario observar mediante microscopía electrónica la microestructura del nuevo material y compararla con la del sensor comercial.

38 ESTUDIO Y CARACTERIZACIÓN DE LOS SENSORES

UNIVERSIDAD POLITÉCNICA DE MADRID ESCUELA TÉCNICA SUPERIOR DE INGENIEROS INDUSTRIALES

### 3.3.2. Diseño y construcción del banco de pruebas

Como se ha visto en el punto anterior, los sensores ya no se comportaban de la forma original, sino que lo hacían de manera muy diferente. Es por ello que no se procedió a realizar el conexionado final hasta que no se hubo caracterizado correctamente.
Para caracterizar el sensor de forma correcta y precisa era necesario diseñar y fabricar un banco de pruebas que estirara el sensor de manera constante y midiera los valores de tensión para cada variación de longitud. De esta forma, el banco de actuación a emplear debía cumplir con los siguientes requisitos:

Contar con longitud suficiente como para alcanzar deformaciones longitudes que se acerquen a la saturación del sensor. El desplazamiento necesario para alcanzar dicha saturación se determinó de forma experimental con un estirado manual previo a la construcción del banco de pruebas y debía estar en torno a los 15 o 20 cm.

Contar con un medio que estire y devuelva a la posición inicial al sensor de forma controlada, continua y uniforme.

Contar con un punto de anclaje del sensor.

Contar con dos puntos para cerrar el circuito eléctrico a través del sensor.

Para cumplir el segundo objetivo, que es el más crítico, se pensó inicialmente en emplear un actuador lineal para esta tarea. Estos actuadores cuentan con un motor que mueve un vástago con una carrera variable. Así se logra de manera muy sencilla y eficaz un movimiento longitudinal.
Sin embargo, estos actuadores presentan ciertos inconvenientes, como su coste y, especialmente, la longitud que presentan cuando el émbolo se ha desplazado hasta su máximo. Estas razones explican el posterior rechazo de esta idea, pues la longitud que presentaría un actuador lineal de 20 cm de vástago sería de aproximadamente 60 cm, lo cual es inviable si a eso se le suma la longitud del propio sensor.
Es por ello que se procedió a idear una nueva forma de lograr este objetivo. A continuación se describen los pasos tomados para realizar este diseño:
1. Sistema de actuación
Para este fin se dispuso de un motor paso a paso o stepper, ya adquirido previamente, en cuyo extremo se había montado un engranaje. De esta forma, gracias al giro del motor paso a paso se puede desplazar una cremallera empujada por el engranaje del eje del motor, logrando así un par piñón-cremallera. Dado que la altura del stepper es de 40 mm (a lo que hay que sumar la base de apoyo de 4 mm de espesor), se diseñó un engranaje de 30 mm de diámetro primitivo que junto a una cremallera de altura de línea primitiva respecto a la base de 5 mm y un pequeño bloque de

CARACTERIZACIÓN DEL COMPORTAMIENTO DE LOS SENSORES 39

TRABAJO FIN DE GRADO
SENSORIZACIÓN Y CONTROL DE UN ROBOT BLANDO MANIPULADOR - RAÚL MOLINA GÓMEZ

madera de 4 mm de altura que facilita tanto el guiado como el deslizamiento de la cremallera, cubren perfectamente la mitad de la altura del motor según: H
2 +hbase =

Φ
2 + hcrem + hapoyo_cremallera. En la figura 3.7 se aprecian tanto el piñón como la cremallera empleados.
(a) Piñón | (b) Cremallera

Figura 3.7 Par piñón-cremallera empleado en el banco de pruebas para caracterizar el comportamiento de los sensores. Fuente: elaboración propia

2. Base del banco de actuación
Con el diseño de la parte actuadora realizado, el siguiente paso a realizar era encontrar un lugar donde posicionar dicho motor con piñón-cremallera. Para ello, se dispuso de un tablón de madera de 460x200x16mm, de esta forma se tenía la suficiente longitud para alcanzar la saturación del sensor a la vez que se aportaba robustez al conjunto.
3. Sistema de anclaje de todos los elementos
Para la correcta fijación de todos los elementos a la base se diseñó un sistema de sujeción del motor stepper (figura 3.8). Para su posterior fijación en la base, se taladraron 4 agujeros de 6.5 mm de diámetro, lo que garantizaba un correcto posicionamiento, junto a pernos de M6. Se usaron además tornillos de M2.5 para anclar el soporte al motor.

Figura 3.8 Base de apoyo para anclar y fijar el motor paso a paso en el banco de pruebas. Fuente: elaboración propia

40 ESTUDIO Y CARACTERIZACIÓN DE LOS SENSORES

UNIVERSIDAD POLITÉCNICA DE MADRID ESCUELA TÉCNICA SUPERIOR DE INGENIEROS INDUSTRIALES

Como punto de anclaje del extremo fijo del sensor se taladró de nuevo un agujero de 6.5 mm a una distancia de 295 mm, que resulta de la suma de la longitud del sensor a la medida necesaria para su uso en el robot y la longitud de la cremallera diseñada. Así, mediante el uso de un perno de M6, se fija la posición del extremo del sensor gracias al uso de dos arandelas que, con la presión ejercida por la tuerca al ser roscada sobre el tornillo, mantienen al sensor en correcta posición. Este sistema de fijación se puede ver en la figura 3.9.

Figura 3.9 Sistema de anclaje del extremo fijo del sensor a probar. Fuente: elaboración propia

4. Mejoras en el diseño y conexionado del sensor
Para finalizar la parte constructiva, era necesario realizar el conexionado del sensor con el hardware de medida. Para ello se emplearon dos cables con pinzas de cocodrilo en sus extremos y un empalme de cables. Este último se pegó a la cremallera en un lateral. De esta forma permitía el anclaje del extremo móvil del sensor a la cremallera. Con todo esto, el conexionado consistía en colocar una de las pinzas de cocodrilo directamente sobre el extremo fijo del sensor mientras que el otro extremo se anclaba a la cremallera con el uso de un empalme de cables mencionado anteriormente. Así, en la otra entrada del conector se colocaba un cable al que iba sujeto por su extremo posterior la pinza de cocodrilo restante. Lo descrito aquí se puede ver en la figura 3.10.
(a) Detalle de la conexión de la conexión del extremo fijo del sensor
(b) Detalle de la conexión de la conexión del extremo móvil del sensor

Figura 3.10 Detalles de las conexiones de ambos extremos del sensor a caracterizar. Fuente: elaboración propia

CARACTERIZACIÓN DEL COMPORTAMIENTO DE LOS SENSORES 41

TRABAJO FIN DE GRADO
SENSORIZACIÓN Y CONTROL DE UN ROBOT BLANDO MANIPULADOR - RAÚL MOLINA GÓMEZ

A su vez, se incorporó una guía (figura 3.11) que impedía el movimiento lateral de la cremallera, evitando posibles desconexiones con el engranaje del piñón.

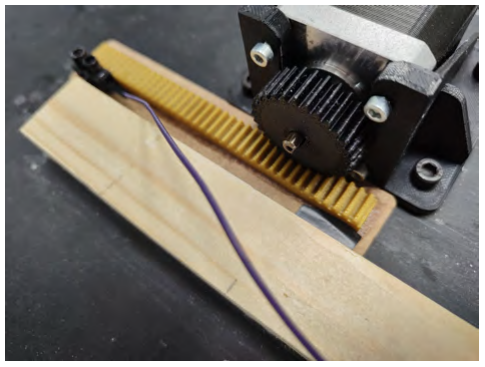
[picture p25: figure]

Figura 3.11 Guía para evitar el movimiento lateral de la cremallera. Fuente: elaboración propia

5. Escritura del código de control
Finalmente, tras el montaje del banco de pruebas se procedió a la escritura del software de control en la IDE de Arduino.

El funcionamiento del banco de actuación consiste en mover paso a paso el stepper a la vez que se leen las medidas realizadas por el INA3221. Tras ello, se enviaban los datos extraídos a través de la comunicación serie (UART) con una App de MATLAB, realizada a través de la herramienta App Designer presente en este software. De esta forma se podrían procesar y almacenar de forma más sencilla y segura. Cada ciclo de prueba consistía en estirar y devolver a la posición inicial el sensor únicamente con la acción del motor paso a paso (sin liberar el sensor en ningún momento).

El banco de pruebas ya montado se puede observar en la figura 3.12, junto a sus conexiones para la prueba.

(a) Banco de pruebas montado y listo para su funcionamiento. Fuente: elaboración propia
(b) Conexiones y elementos necesarios para el uso del banco de pruebas. Fuente: elaboración propia

Figura 3.12 Banco de pruebas para la caracterización de los sensores. Fuente: elaboración propia

42 ESTUDIO Y CARACTERIZACIÓN DE LOS SENSORES

UNIVERSIDAD POLITÉCNICA DE MADRID ESCUELA TÉCNICA SUPERIOR DE INGENIEROS INDUSTRIALES

### 3.3.3. Conclusiones extraídas del comportamiento de los sensores

Una vez diseñado, construido y programado el banco de pruebas, se procedió a realizar la caracterización de los sensores. Los resultados obtenidos de los experimentos realizados a temperatura ambiente (25ºC) con los distintos sensores se pueden observar en la figura
3.13. Se emplearon dos sensores diferentes, todos ellos empleando el mismo procedimiento. De esta forma se puede comparar si presentan un comportamiento similar o no. Las medidas de tensión se hicieron con una tensión de bus de 12V, pues es más seguro emplear 12V que 24V y no necesitamos aquí resolución.

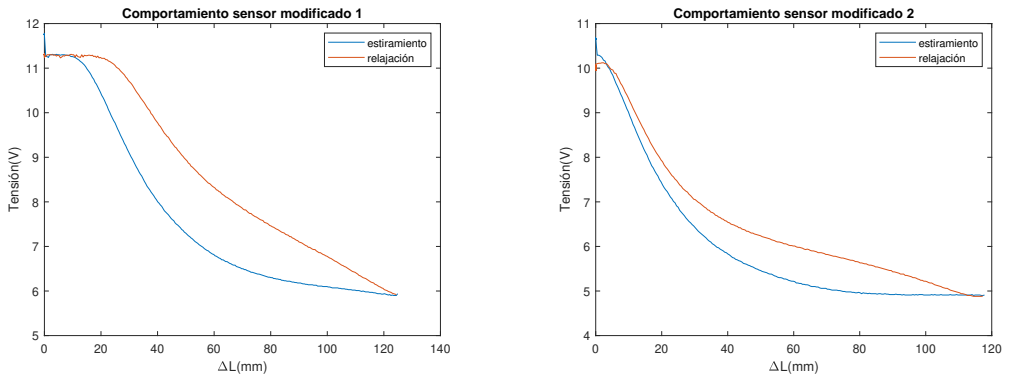
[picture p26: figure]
Tensión(V); Comportamiento sensor modificado 1; estiramiento; relajación; Comportamiento sensor modificado 2

(a) Comportamiento del sensor 1
(b) Comportamiento del sensor 2

Figura 3.13 Comportamiento ante la elongación de dos sensores modificados distintos. Fuente: elaboración propia

De aquí se extraen las siguiente conclusiones:

1. Los sensores modificados presentan un rango muy amplio de medición hasta la saturación.
2. Los sensores modificados presentan cuatro zonas claramente diferenciadas:
a) Zona umbral: Al comienzo, en un rango variable de 0 a 10 mm no se aprecian cambios en la medida de los sensores.
b) Zona lineal: Tras la zona umbral, el sensor presenta una zona lineal variable de entre 20 a 30 mm.
c) Zona exponencial: Posterior a la zona lineal y previo a la saturación, el sensor presenta un perfil curvo similar al presentado por las funciones exponenciales.
d) Zona de saturación: Finalmente, llegado cierto valor variable, el sensor satura su medida y no se aprecian variaciones en valores medidos.
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

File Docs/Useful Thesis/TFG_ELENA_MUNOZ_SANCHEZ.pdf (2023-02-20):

# CONSTRUCCIÓN Y CONTROL DE UN ROBOT CONTINUO DE CABLES CON

# DISCOS PIVOTANTES

FEBRERO 2022

# Elena Muñoz Sánchez

DIRECTOR DEL TRABAJO FIN DE GRADO:

## Antonio Barrientos Cruz

## Elena Muñoz Sánchez

### TRABAJO FIN DE GRADOPARA LA OBTENCIÓN DEL TÍTULO DE GRADUADO EN INGENIERÍA EN TECNOLOGÍAS INDUSTRIALES

“Más vale tarde que nunca”

“Algún día diré: No fue fácil, pero lo logré”

ELENA MUÑOZ SÁNCHEZ | V

AGRADECIMIENTOS

En primer lugar, quiero agradecer a mi familia su apoyo y amor incondicional durante estos largos años. Sin vosotros no estaría donde estoy ni habría llegado a ser quien soy ahora.

A mi tutor, Antonio, por creer en mí a lo largo de todo el proyecto más que yo misma, y apoyarme en todas las dudas e impedimentos que me he ido encontrando.

A mis dos grandes mentores, Iván y David, por mostrarme este proyecto y guiarme siempre que lo he necesitado.

A mi compañero Jaime, por ayudarme a materializar el Pylori-I y aguantarme en los peores momentos.

A la asociación de estudiantes RESET, por todo lo que me ha aportado estos últimos años, tanto académica como profesionalmente.
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

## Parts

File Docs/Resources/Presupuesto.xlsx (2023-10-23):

Concepto | Coste unitario | Cantidad | Importe
Hardware copias de seguridad | 500 € | 1 | 500.00 €
Maleta trasporte robot | 150.00 € | 1 | 150.00 €
Conexión HDMI | 15.00 € | 1 | 15.00 €
Subtotal material |  |  | 665.00 €
Concepto | Coste total | Años | Importe
Ordenador portátil ASUS GL752VW | 1200 € | 5 | 240 €
Robot Unitree A1 + lídar | 15000 € | 10 | 1500 €
Pantalla gráfica Lenovo | 500 € | 10 | 50 €
Subtotal amortizaciones |  |  | 2455.00 €
Concepto | Coste horario | Horas | Importe
Autor del proyecto | 25 € | 330 | 8250 €
Tutor del proyecto | 40 € | 20 | 800 €
Cotutor del proyecto | 30 € | 50 | 1500 €
Subtotal costes personal |  |  | 10550.00 €
Totales |  |  | Importe total
Material |  |  | 665.00 €
Amortizaciones |  |  | 2455.00 €
Personal |  |  | 10550.00 €
Costes indirectos |  | 15% | 2050.50 €
IVA |  | 21% | 3301.30 €
Total |  |  | 19021.81 €

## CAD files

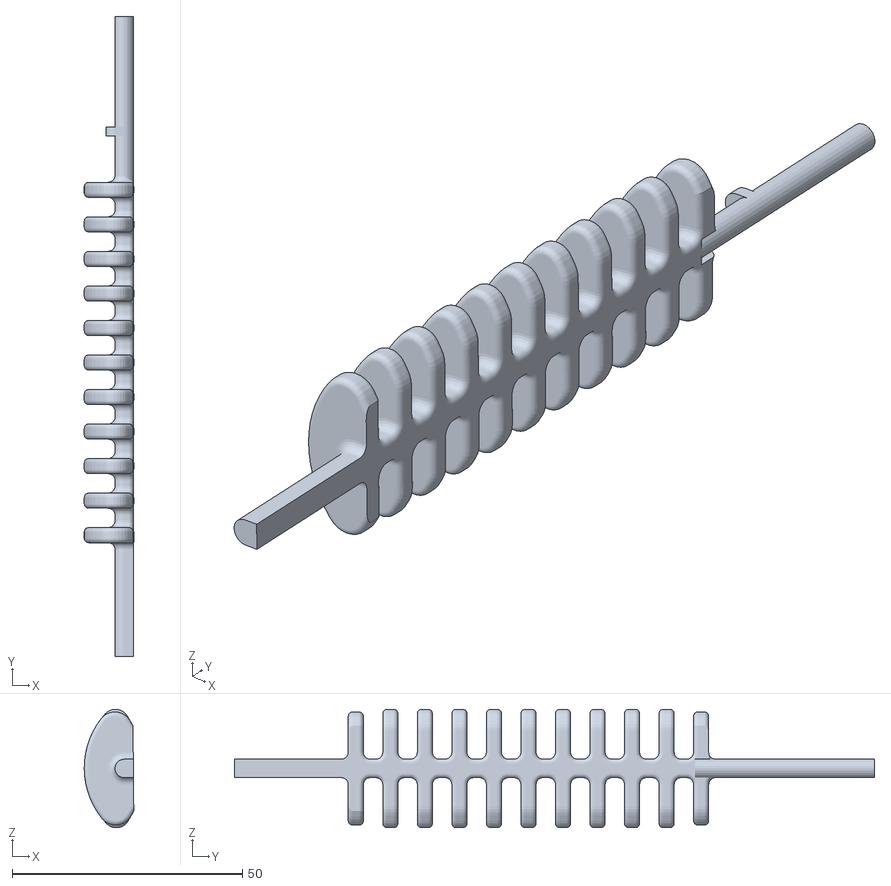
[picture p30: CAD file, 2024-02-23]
CAD/Ficheros_Fusion360/Macho v2.stl
10.8 x 139.0 x 25.7

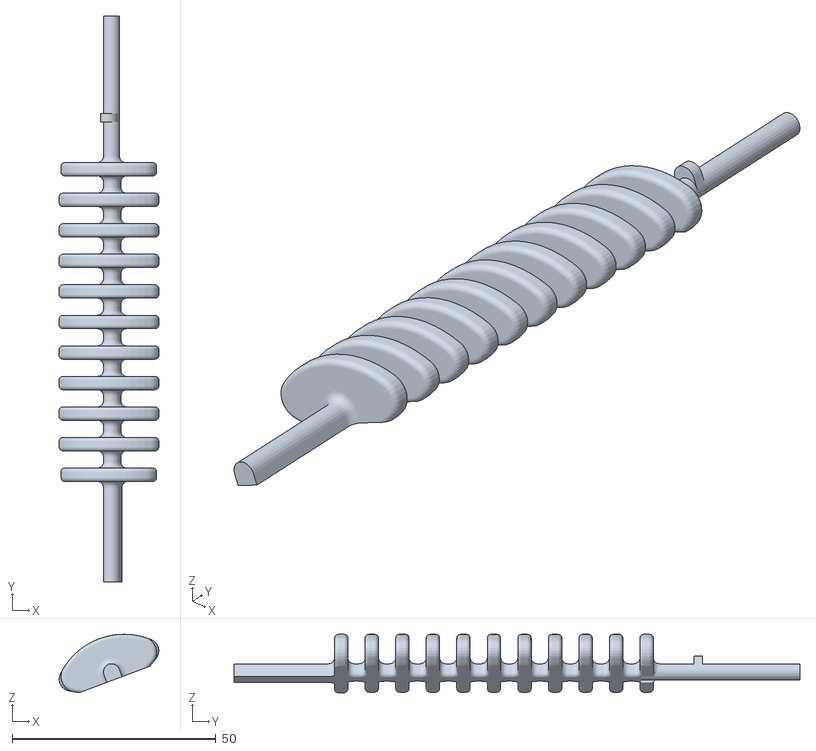
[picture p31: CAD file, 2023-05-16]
CAD/STL_moldefinal/macho.stl
24.5 x 139.0 x 14.4

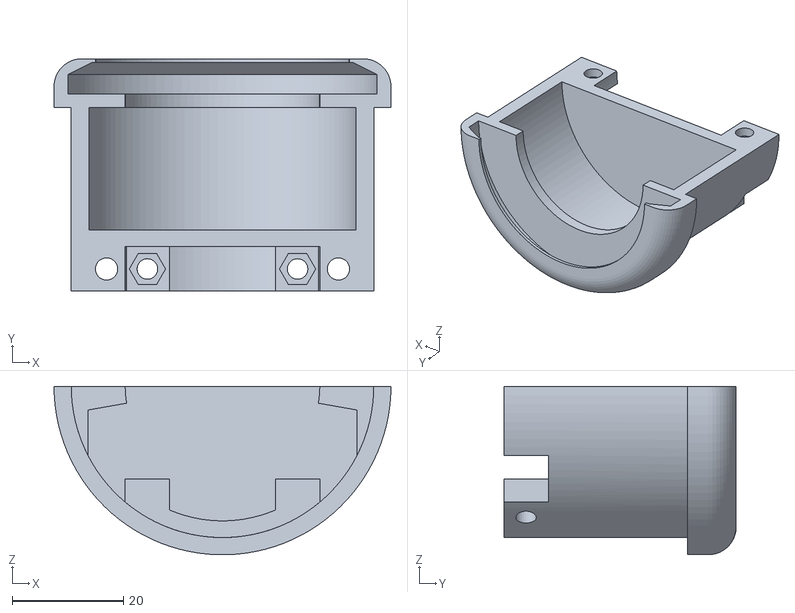
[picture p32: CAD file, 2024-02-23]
CAD/Ficheros_Fusion360/Robot_version_final_pesos_macho_2 v3.stl
60.6 x 41.8 x 30.3

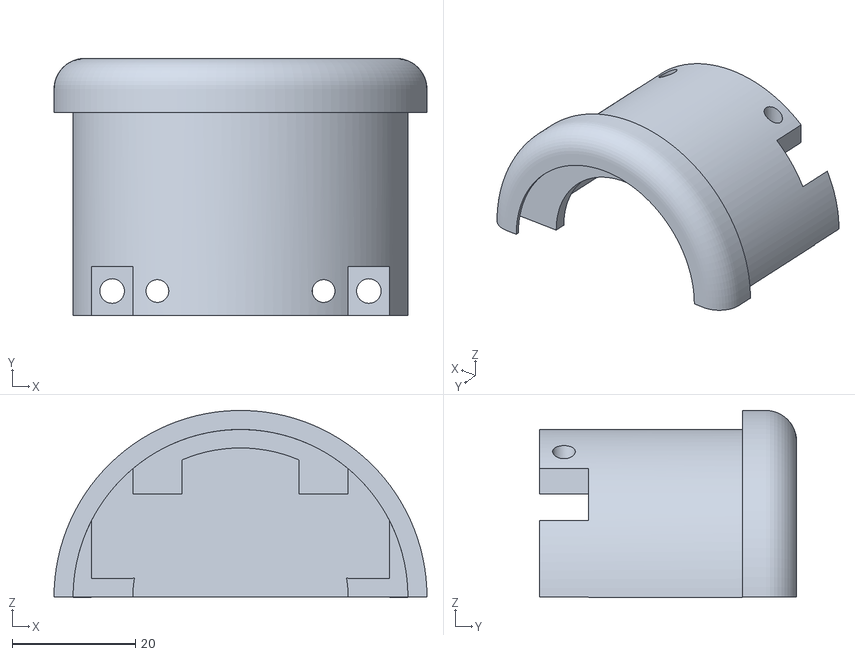
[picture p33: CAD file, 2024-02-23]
CAD/Ficheros_Fusion360/Robot_version_final_pesos_macho_1 v4.stl
60.6 x 41.8 x 30.4

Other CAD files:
CAD/Ficheros_Fusion360/Molde_final_utilizado v3.f3z
CAD/Ficheros_Fusion360/SoftControl_assembly v2.f3z

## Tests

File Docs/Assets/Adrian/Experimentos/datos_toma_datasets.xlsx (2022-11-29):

Dataset: | 1 | 2 | 3 | 4 | 5 | 6 | 7
N. Muestras | 50 | 50 | 50 | 250 | 3 | 100 | 100
Tiempo (s) | 347.66 | 348.69 | 356.32 | 1942.23 | 19.42 | 605.41 | 599.88
Tiempo/Muestra | 6.9532 | 6.9738 | 7.1264 | 7.76892 | 6.473333333 | 6.0541 | 5.9988
Tiempo medio por muestra: | 6.764079048
Varianza: | 0.3991644606

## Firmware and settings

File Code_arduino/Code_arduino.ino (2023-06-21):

#include "Config.h"
#include "RobotSegment.h"
#include "Valvula.h"

#define P_V_RATIO (8.7 - 9) / 400

// ############### Objetos globales ################

// Numero de valvulas. Se considera valvula al conjunto de una 22 + una 23

// Sensores elasticos
const uint8_t num_inas = 1;
Robot::myINA *ina[num_inas];
ina3221_addr_t addresses[num_inas] = {INA3221_ADDR40_GND};

INA3221 ina_0(INA3221_ADDR40_GND);

// Si se trabaja con robot real o con modelo (el dato lo manda Matlab, aunque por seguridad se dice que modelo)
uint8_t real_robot = 0;
const float length_constant = 0.05;

// Modo normal
modos State = S_NORMAL;

const uint32_t calibration_millis = 5000;

// Variable de estado
char cmode;
long int t = 0;
long int t1 = 0;
double datos[3];
int x = 0;

// Array de valvulas
Valvula *misValvulas[NUM_VALVULAS];


//Interrupcion emergencia
void emergency_stop_callback()
{
  State = S_ERROR_PARADA_EMERGENCIA;
  for(uint8_t i = 0; i < NUM_VALVULAS; i++)
  {
    misValvulas[i] -> alAire();
  }

}


void current_measure_init() {
    ina_0.begin(&Wire);
    ina_0.reset();
    ina_0.setShuntRes(100, 100, 100);
}

void setup()
{

  // Comunicacion con el PC
  Serial3.begin(9600);

  // Comunicacion con ESP32 (Interfaz wifi para desarollo)
  //Serial2.begin(9600);
  
  // Inicializamos los pines de la marca de la vision por omputador
  pinMode(PIN_LED_R, OUTPUT);
  pinMode(PIN_LED_G, OUTPUT);
  pinMode(PIN_LED_B, OUTPUT);


  //attachInterrupt(digitalPinToInterrupt( EMRGY_PIN), emergency_stop_callback, CHANGE);
  pinMode(EMRGY_PIN, INPUT_PULLUP);

  // Instanciamos las valvulas
  for (int i = 0; i < NUM_VALVULAS; i++)
  {
    misValvulas[i] = new Valvula(PIN_32_ARRAY[i], PIN_22_ARRAY[i]);
  }

  // Inicilaizamos las valvulas
  for (int i = 0; i < NUM_VALVULAS; i++)
  {
    misValvulas[i]->init();
  }


  pinMode(LED_BUILTIN, OUTPUT);
  pinMode(2, OUTPUT);

  // Inicializamos los sensores
  digitalWrite(LED_BUILTIN, HIGH);
  /*for (uint8_t i = 0; i < num_inas; i++) {
    Robot::myINA ina0;
    ina0 = Robot::myINA(INA3221_ADDR40_GND, 1);
    ina[i] = &ina0;
    ina[i] -> current_measure_init();
  }*/
  
  Wire.begin();
  current_measure_init();

  t = millis();

  /*
  // Calibracion de los sensores
  while(millis() - t < calibration_millis) {
    sensor1.calibrate();
    sensor2.calibrate();
    sensor3.calibrate();
  }
  */
  digitalWrite(LED_BUILTIN, LOW);

  // Se imprimen por Serial los valores calibrados de los sensores
  /*Serial3.print(sensor1.getMaxCalibratedValue());
  Serial3.print(" ");
  Serial3.println(sensor1.getMinCalibratedValue());
  Serial3.print(sensor2.getMaxCalibratedValue());
  Serial3.print(" ");
  Serial3.println(sensor2.getMinCalibratedValue());
  Serial3.print(sensor3.getMaxCalibratedValue());
  Serial3.print(" ");
  Serial3.println(sensor3.getMinCalibratedValue());*/
  Serial3.println("Calibration done");

  t = millis();

  // Modo normal
  State = S_NORMAL;
  // delay(1000);
}

void loop()
{
  if(State == S_NORMAL)
  {
  
  t1 = millis();

  if (Serial3.available() > 0)
  {
    static char op = ' ';
    op = Serial3.read();
    int num_valv;
    //int x;
    float p;
    int buffer[NUM_VALVULAS + 1];
    switch (op)
    {

    // decir si trabajamos con un robot real o ficticio
    case 'i':
      real_robot = Serial3.parseInt();
      Serial3.println("Working mode changed");
      break;

    // abrir valvula
    case 'a':
      num_valv = Serial3.parseInt();
      Serial3.println(num_valv);
      misValvulas[num_valv]->alAire();
      break;

    // cerrar valvula
    case 'b':
      num_valv = Serial3.parseInt();
      misValvulas[num_valv]->Cerrada();
      break;

    // a presion
    case 'c':
      num_valv = Serial3.parseInt();
      misValvulas[num_valv]->Presion();
      break;

    // llenar durante x ms
    case 'f':
      num_valv = Serial3.parseInt();
      x = Serial3.parseInt();
      misValvulas[num_valv]->fill_millis((uint16_t)x);
      break;

    // vaciar durante x ms
    case 'e':
      num_valv = Serial3.parseInt();
      x = Serial3.parseInt();
      misValvulas[num_valv]->emptyng_millis((uint16_t)x);
      break;

    // Medir los valores de los sensores
    case 'M':
      Serial3.print("M ");
      if (real_robot) {
        /*for (uint8_t i = 0; i < num_inas; i++) {
          ina[i]->measure();
        }*/
        Serial3.print(ina_0.getVoltage(INA3221_CH1));
        Serial3.print(" ");
        Serial3.print(ina_0.getVoltage(INA3221_CH2));
        Serial3.print(" ");
        Serial3.println(ina_0.getVoltage(INA3221_CH3));
      } else {
        for (uint8_t i = 0; i < NUM_VALVULAS; i++) {
          int p = misValvulas[i]->get_actual_pressure();
          Serial3.print(9 + p * P_V_RATIO);
          Serial3.print(" ");
        }
      }
      Serial3.println(" ");
    break;

    // Para escribir un dato para todas las valvulas en modo absoluto
    case 'w':
    
      for (int i = 0; i < NUM_VALVULAS + 1; i++)
      {
        buffer[i] =  Serial3.parseInt();
      }

      for (int i = 1; i < NUM_VALVULAS + 1; i++)
      {
        if (buffer[0])
        {
          if (buffer[i] >= 0)
          {
            misValvulas[i - 1]->fill_millis(buffer[i]);
          }
          else
          {
            misValvulas[i - 1]->emptyng_millis(-buffer[i]);
          }
        }
        else
        {
          misValvulas[i - 1] -> relC(buffer[i]);
        }
      }

      break;

      // Para cambiar el brillo de las luces r,g,b de la marca de la vision por computador
      case 'v':
      case 'V':
        
        // rgb
        num_valv = Serial3.parseInt();
        x = Serial3.parseInt();
        switch(num_valv)
        {
          // r
          case 1:
            analogWrite(PIN_LED_R, x > 0? (x > LED_MAXV_R? LED_MAXV_R : x  ) : 0 );
          break;
          // g
          case 2:
            analogWrite(PIN_LED_G, x > 0? (x > LED_MAXV_G? LED_MAXV_G : x  ) : 0 );
          break;
          // b
          case 3:
            analogWrite(PIN_LED_B, x > 0? (x > LED_MAXV_B? LED_MAXV_B : x  ) : 0 );
          break;
        }

      break;

     

      // Para cambiar la presion maxima en modo relativo
      case 'l':
        p = Serial3.parseFloat();
        for (int i = 0; i < NUM_VALVULAS; i++)
        {
          misValvulas[i] ->  set_max_rel_pressure(p);
        }

      break;

      // Para cambiar ratio inflado/desinflado
      case 'm':
        p = Serial3.parseFloat();
        for (int i = 0; i < NUM_VALVULAS; i++)
        {
          misValvulas[i] ->  set_mult(p);
        }

      break;

    // Modo relativo en una sola valvula
    case 'x':
      num_valv = Serial3.parseInt();
      x = Serial3.parseInt();
      misValvulas[num_valv]->relC(x);
      break;

    case 'k':
      
      for(int i = 0; i < NUM_VALVULAS; i++)
      {
        int pres = Serial3.parseInt();
        misValvulas[i]->relC( pres);
        Serial3.print(i);
        Serial3.print(" ");
        Serial3.println(pres);

        delay(2);
      }
      
    break;

    
    }
  }


  // Callback de las valvulas   
  for (uint8_t i = 0; i < NUM_VALVULAS; i++)
  {
    misValvulas[i]->callback();
  }

  // Comunicacion con ESP32
  /*if (Serial2.available() > 0)
  {

    static char op = ' ';
    op = Serial3.read();
    Serial3.println(op);
    int num_valv;

    switch (op)
    {
    // abrir valvula
    case 'a':
      num_valv = Serial2.parseInt();
      Serial3.println(num_valv);
      misValvulas[num_valv]->alAire();
      break;

    // cerrar valvula
    case 'b':
      num_valv = Serial2.parseInt();
      misValvulas[num_valv]->Cerrada();
      break;

    // a presion
    case 'c':
      num_valv = Serial2.parseInt();
      misValvulas[num_valv]->Presion();
      break;
    }
  }*/

  
  // Comprobamos si alguna valvula ha entrado en modo de parada de emergencia
   for(uint8_t i = 0; i < NUM_VALVULAS; i++)
   {
    if(misValvulas[i]-> getEmergency() == true)
    {
      State = S_ERROR_STOPAUTO;
    }
    
   }
  
  
  }
 
  


  if(State == S_ERROR_STOPAUTO)
  {
    // Parpadea el led
    digitalWrite(13, !digitalRead(13));
    delay(100);

    if( Serial3.available() > 0)
    {
      char op = Serial3.read();

      // Rearmamos
      if(op == 'R')
      {
        for (int i = 0; i < NUM_VALVULAS; i++)
        {
          misValvulas[i] -> rearmar();
          State = S_NORMAL;
        }
      }

    }

  }

  
}

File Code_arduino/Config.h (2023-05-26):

//En este fichero se declararan todas las constantes del programa, definiciones de tipos
// etc.

#ifndef _CONFIG_H_
#define _CONFIG_H_



#include <Arduino.h>
#include <Wire.h>
#include <SPI.h>
#include "Pinout.h"
#include "Config.h"
#include "SerialCommunication.h"


#define SCREEN_WIDTH 128 // OLED display width, in pixels
#define SCREEN_HEIGHT 64 // OLED display height, in pixels
#define SCREEN_ADDRESS 0x3C // OLED I2C address
#define OLED_RESET -1 // Reset pin # (or -1 if sharing Arduino reset pin)

enum modos
{
    S_NORMAL,
    S_ERROR_STOPAUTO,
    S_ERROR_PARADA_EMERGENCIA
};

const uint8_t LED_MAXV_R = 180;
const uint8_t LED_MAXV_G = 255;
const uint8_t LED_MAXV_B = 180;


#endif // _CONFIG_H_

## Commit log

2022-11-15 ficheros cad z link del video de fabricacion al readme
    [Molde_final_utilizado v3.f3z, SoftControl_assembly v2.f3z]
2022-12-11 Fotos del caracterizado de sensores
2023-01-19 Funciones propias de filtrado
2023-04-12 Caracterización sensor con fórmula. Sale algo pero regular
2023-04-19 Modelo sensor. No conseguido
2023-05-04 Graficas sensor
2023-05-16 Clase robot con funciones de envío de aire y captura de posición (cero incluido)
2023-05-16 Mejoras clase. readCameraArduino adaptado a clases
    [macho.stl]
2023-05-26 Código Adrián como Arduino y reorganización de la parte de Matlab!
2023-06-02 PID implementado. Falta coordinar Visión
2023-06-02 Reference frame of the cameras is now correct
2023-06-20 Prepared to work with three sensors. PID implemented
2023-07-06 Modificaciones arduino
2023-07-22 Gráficas de error
2023-10-23 Repository Reorganisation
    [Presupuesto.csv, Presupuesto.xlsx, PresupuestoE.csv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]
2023-10-25 PID implemented
2024-02-23 CCD First implementation
    [Macho v2.stl, Presupuesto.xlsx, Robot_version_final_pesos_macho_1 v4.stl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]
2024-05-16 GA finished and working
    [NNSize.xlsx]
